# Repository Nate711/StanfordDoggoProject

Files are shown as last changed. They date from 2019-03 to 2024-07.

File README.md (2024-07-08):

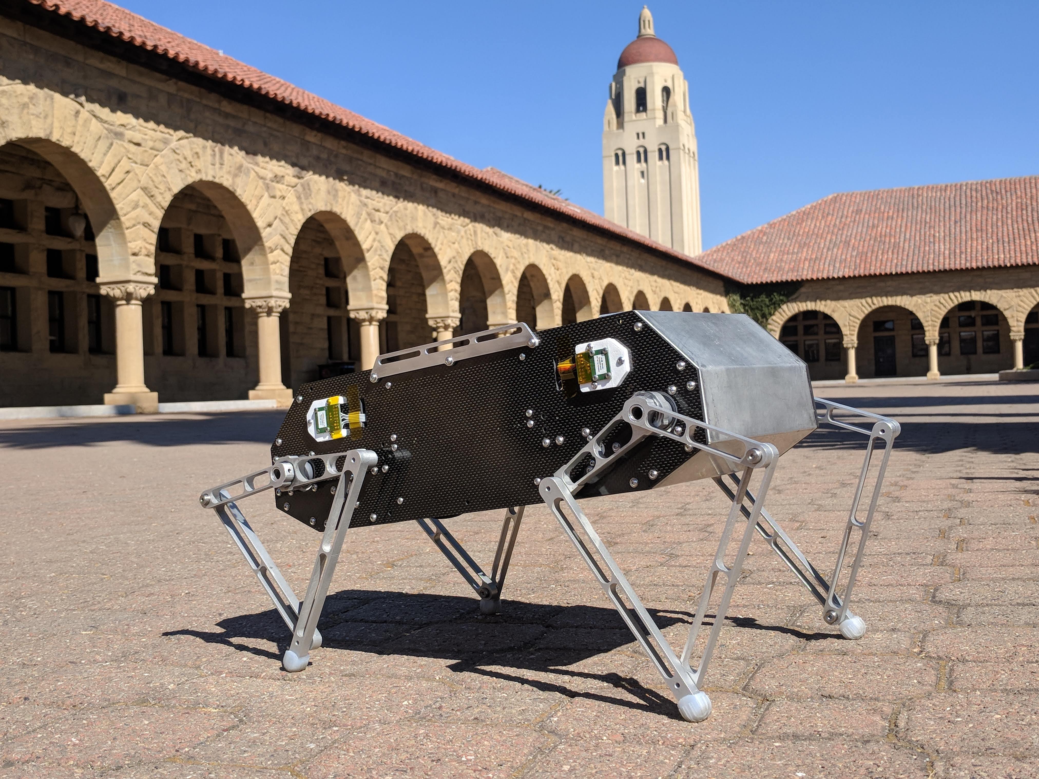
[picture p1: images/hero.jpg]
hero


# End-of-life notice
Thank you everyone for your interest and support over the last 6 years for this project! 

We are hard at work building a new robot, Pupper v3, and so would like to stop supporting this project. Thanks for your understanding! Pupper v3 is fully open source and build instructions will be released in the coming months. You can find preliminary information here https://pupper-v3-documentation.readthedocs.io/en/latest/index.html 







Quick specs for Pupper v3
* Powerful 400W GIM4305 brushless motors
* Raspberry Pi 5
* Reinforcement learning locomotion policy out-of-the-box
* Luxonis SR depth camera
* LCD screen for debugging and facial expressions
* Roughly $1000 BOM

# The Stanford Doggo Project
## Overview Of Stanford Doggo
Stanford Doggo is a highly agile robot designed to be an accessible platform for legged robot research. The robot currently holds the record (among all robots) for the highest vertical jumping agility<sup>1</sup> and can jump twice as high as any existing quadruped robot! Weighing in at a little less than 5kg, Stanford Doggo is easy and safe to develop on, but at the same time, don't expect Stanford Doggo to carry heavy loads or climb super aggressive terrain. If you use a portion of this project or want further technical details, please cite our paper presented at ICRA 2019: https://ieeexplore.ieee.org/document/8794436 (freely available on arxiv: https://arxiv.org/abs/1905.04254). The project is generously supported by Stanford Student Robotics http://roboticsclub.stanford.edu/.

<sup>1</sup>[Vertical jumping agility] = [maximum vertical jump height] / [time from onset of actuation to apogee of jump]

## Building Doggo
We hope you build your own Stanford Doggo! In the Hardware folder of this repository we've linked the Fusion 360 CAD model and it includes all the parts you'll need to source. Many of the custom pieces are either 3d printed or waterjet (instead of manually milled for instance), which means you will only have to do post-processing work. For example, the primary links on each waterjet leg assembly require you to drill and tap a hole for a set screw. If you need help, please reference the CAD, submit an issue to this github repo, or email the owner, nathan kau [at] stanford [dot edu].

You can find a work-in-progress bill of materials here: https://docs.google.com/spreadsheets/d/1MQRoZCfsMdJhHQ-ht6YvhzNvye6xDXO8vhWQql2HtlI/edit#gid=726381752. Please don't hesitate to ask for help!

## Doggo Software
The brains of Stanford Doggo are split between the ODrive motor controllers and the central Teensy microcontroller. To run Doggo, you'll need to flash the our custom ODrive firmware onto the four motor controllers in the robot and then configure them using the doggo_setup.py script included in that repository. Quick note, if you have a different mechanical design than Doggo, make sure to update the gear_ratio parameter in the code or via odrivetool. After uploading the firmware and configuring, you'll next want to upload the Doggo Arduino code to the central microcontroller. This code is responsible for switching between different states and sending the right position commands to the robot. When you power on the robot, the four legs will first do a calibration routine so that the motors and encoders become synced up, and then the robot will enter an idle mode. Once in idle, you can send serial commands over the wireless xbee network to command Doggo to trot, jump, etc. Please reference the Doggo software repo for more information.

## Help
We encourage you to submit issues to this github, or email the owner, nathan kau [at] stanford [dot edu]. 

# A blog post about Doggo
Hi all, I thought I'd share more about the Stanford Doggo Project, which you might have seen in Oskar's New Year's update! We're a group of undergrad and grad students in Stanford Student Robotics and have been working on legged robots for the last year and a half. Our latest robot, Stanford Doggo, is a shoebox-sized quadruped robot that can walk, trot, pronk, and jump around.

I think this video gives the best overview of what Doggo is:

https://www.youtube.com/watch?v=cJxotk4lR90

And my favorite video, Doggo doing a backflip:

https://www.youtube.com/watch?v=aZylPK7SbV0

I&rsquo;ve been seeing a ton of amazing projects here on the forum and on the ODrive Discord channel, so I wanted to make a blog post explaining how Doggo works. I hope people might be able to learn something from this post, and perhaps even build their own Doggo and improve upon it. The whole project is open-source (links below) with CAD, code, and firmware available on Github. The robot code runs on a Teensy 3.5, and we use ODrives for motor control so I imagine a lot of people here could jump right in. We've also tried to make the robot inexpensive to build in your own lab, school, or home, and we absolutely welcome people to contribute to the project. 

## Relevant links:
GitHub project repository: https://github.com/Nate711/StanfordDoggoProject
Full, downloadable Fusion 360 CAD: https://a360.co/2OBxTbH
Teensy code: https://github.com/Nate711/Doggo
ODrive fork: https://github.com/Nate711/ODrive

# Mechanical Design

## Coaxial mechanism
The coaxial mechanism that drives each leg is definitely the most complex mechanical component of the robot. It has also been the most troublesome. The way it works is that we have two TMotor MN5212 motors mounted on the carbon fiber side panel. We also have a 3D printed bearing block that has two bearings to hold the outer coaxial tube. (Refer to the cutaway CAD view below). The two motors transfer power to the coaxial shafts via 6mm wide, 3mm pitch GT2 belts between a 16T pulley and a 48T pulley. We didn&rsquo;t have room in our mass budget for regular, off-the-shelf pulleys, so we printed our own using the Xometry SLS service. As a side note, we learned to always specify to the service that the pulleys must be printed up. If the parts are printed at an angle, the geometry of the pulley teeth gets distorted because of the off-angle layers. Above the pulleys we have a waterjet aluminum bracket to maintain belt tension and thereby prevent skipping during high-torque situations. That said, it was a real pain to find the best center-to-center distance for the bracket because the slop in the connection between the motors and small pulleys, and the slop in the connection between the larger pulleys and the shafts meant that the center-to-center distance for the top bracket had to be 0.5mm larger than the nominal center-to-center distance prescribed by the belt supplier (SDP-SI). The biggest problem with this assembly was that the higher the belt tension, the more friction we had in the assembly. Higher friction means worse tracking performance for the motors, and also worse sensitivity to touch-down events and the like. On our next robot, we&rsquo;re hoping to have smoother, more precisely machined pulleys, and less slop in the coaxial assembly.

#### CAD diagram
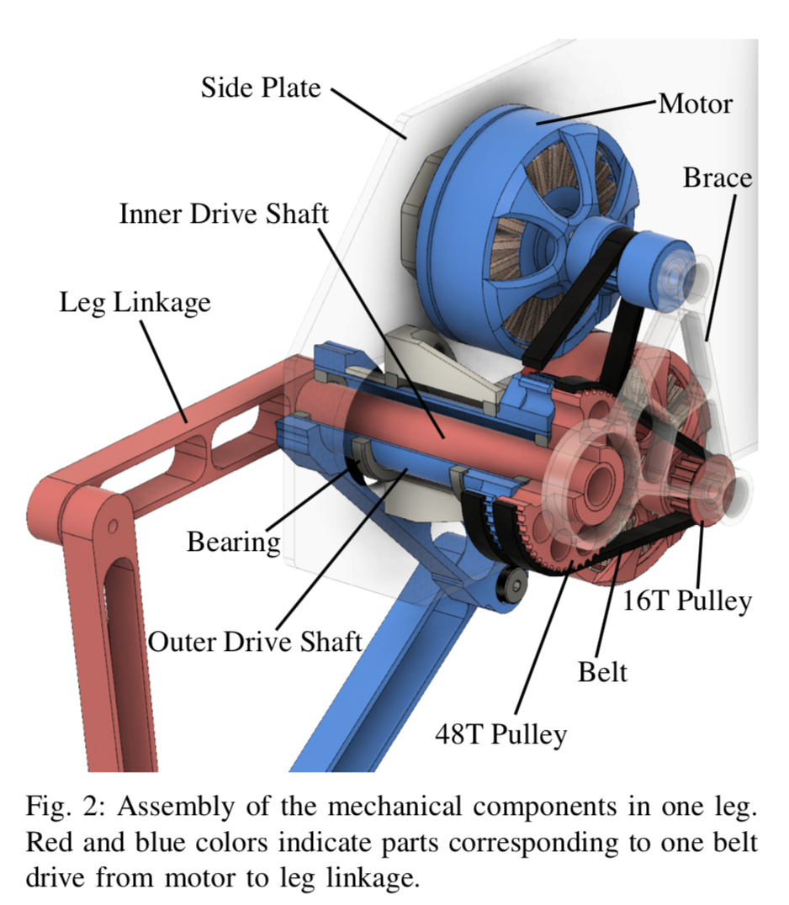
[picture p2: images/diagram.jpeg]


#### IRL
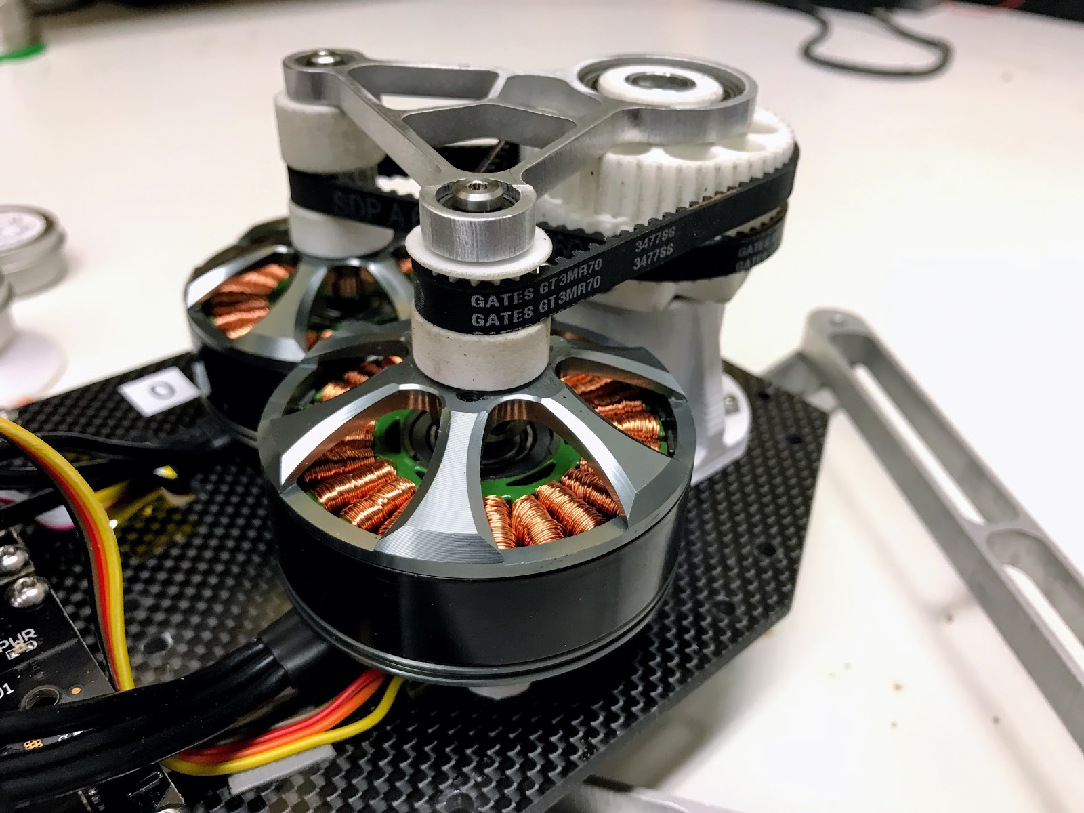
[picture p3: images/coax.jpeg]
diagram


#### In operation
https://www.youtube.com/watch?v=6PL3aur4g4c

## Legs

Doggo has four, 2DOF legs of the SCARA flavor. By SCARA flavor I mean that each leg is a five bar linkage and the two upper links are driven co-axially. The actual leg links were waterjet cut by Big Blue Saw, which is a great online service (although make sure to upload all your parts in one DXF to save money). The waterjet parts were actually precise enough that we did not need to ream the holes for the bearings.

### Joints
For each joint, there are two deep groove ball bearings stacked next to each other in on link, and a shoulder bolt goes through them and threads into the opposing link.

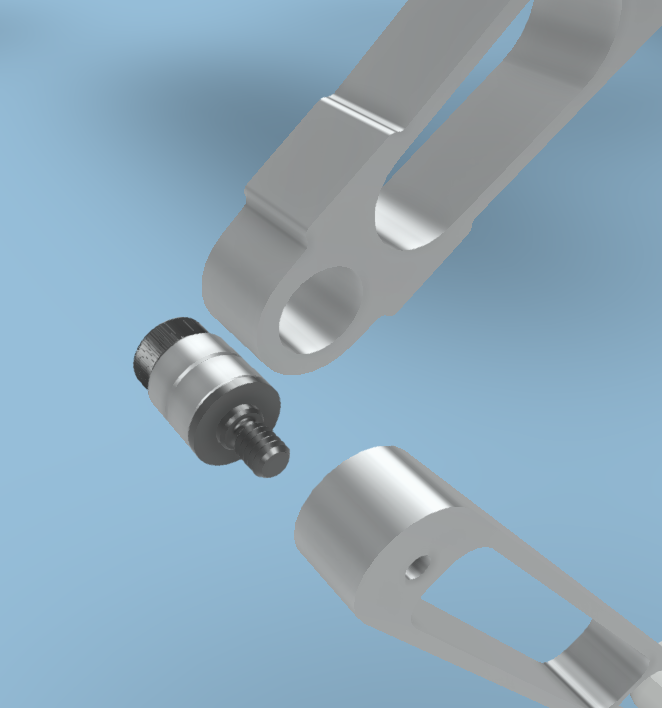
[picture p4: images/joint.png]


### Feet
The robot feet are silicone pieces that we made using a 3D printed, 2-part mold.

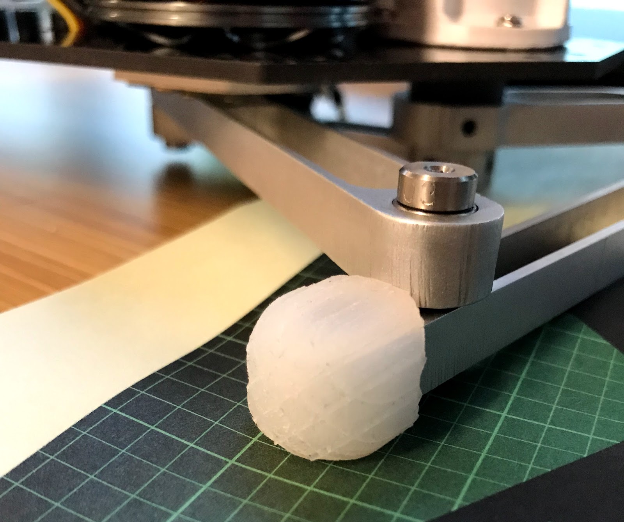
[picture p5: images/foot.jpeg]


## Frame

The frame of the robot is thankfully very simple. We have two waterjet, 4mm carbon fiber panels on each side, connected by two 1/32&rdquo; 5052 aluminum sheet metal parts. These sheet metal parts were cut using a waterjet, and then folded up by hand (long story, but because the two carbon fiber panels are canted inwards, the tabs on the aluminum part couldn&rsquo;t be folded on a brake).

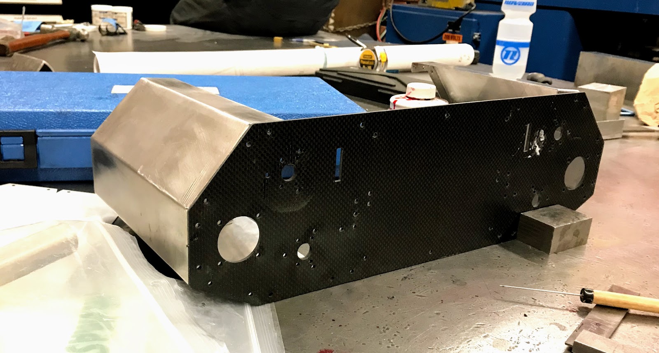
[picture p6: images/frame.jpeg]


# Electronics
Doggo has four v3.5, 48V ODrives, two for each leg, mounted on the carbon fiber side panels. Sitting on a 2mm carbon fiber plate in the middle, we have a Teensy 3.5, a Sparkfun BNO080 IMU, and a 5mW Xbee. The Teensy talks to the ODrives over four separate UART lines, each operating at 500,000 baud. Underneath this plate, we have the power distribution board (a janky quadcopter PDB we found on Amazon), and a fancy Gigavac P105 Mini-Tactor relay so we can kill the robot power using an offboard ESTOP switch. We also put our two, 1000mah 6s Tattu lipo batteries down there.

Last, but not least, each motor has a AS5047P encoder to track the motor angle. We actually are only using the incremental interface, because at the time we built the robot, there was no absolute encoder support on the ODrive and we couldn&rsquo;t make the index pin functionality work either.

#### Electronics schematic
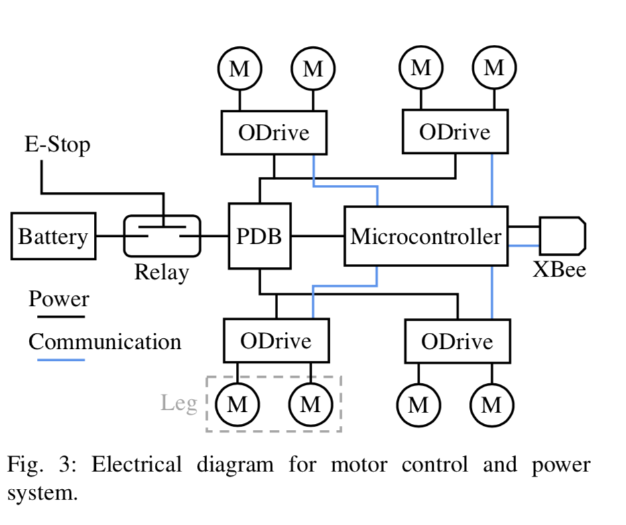
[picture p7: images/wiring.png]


#### Layout of ODrives
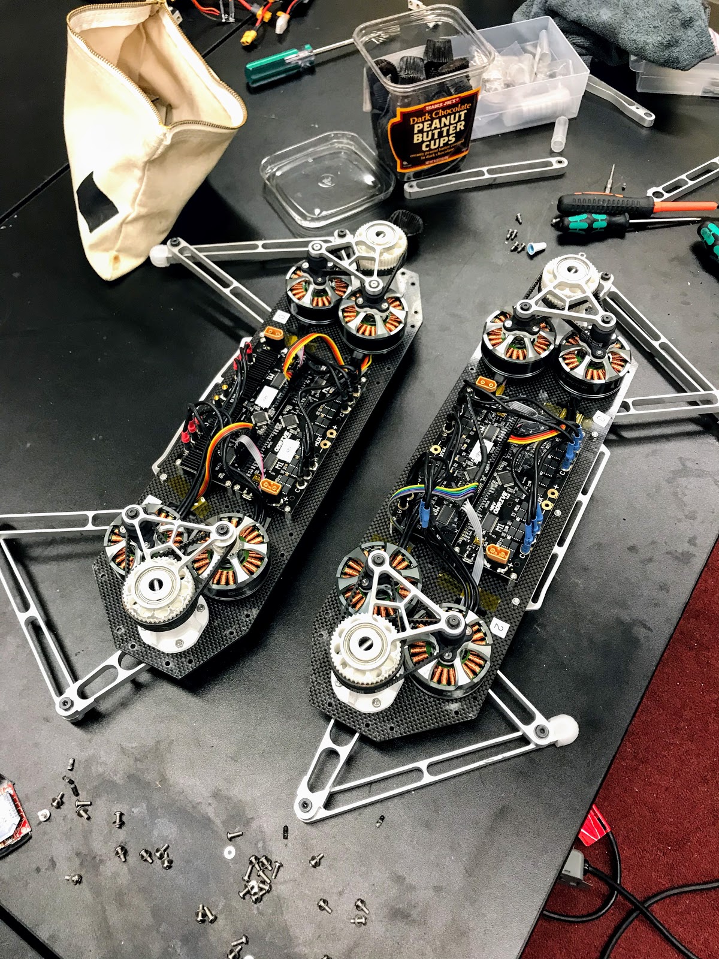
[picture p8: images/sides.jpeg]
|394x526


#### Top side of the middle electronics plate
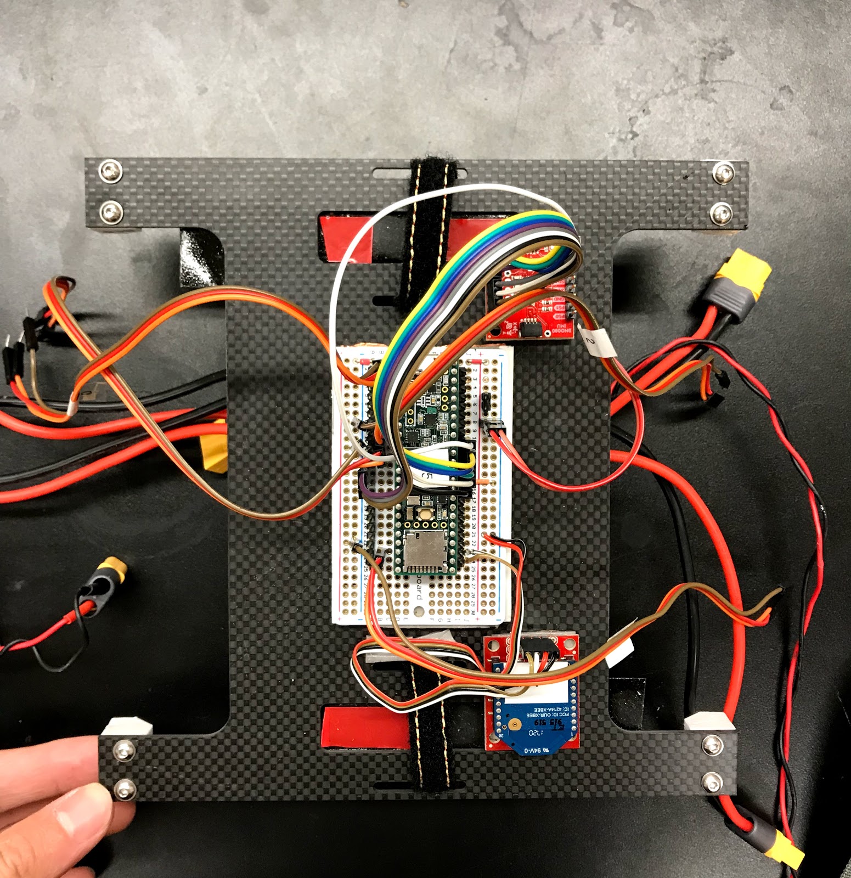
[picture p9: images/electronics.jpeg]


#### The belly of the robot: Relay (translucent piece in the middle), PDB (golden board in front of the relay), and batteries (close and far).
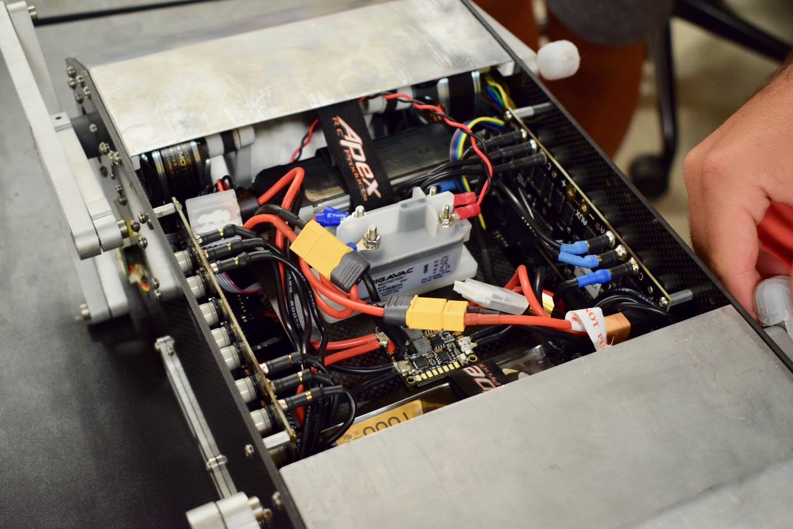
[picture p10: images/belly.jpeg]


# Software

## Overview

The Doggo software is relatively simple as far as things go. The gist of it is that we have a state machine that flips between different behaviors (like trot, jump etc), and for each behavior we send different position commands and gains to the four ODrives. We also have some helper threads running, like one to take IMU measurements, another to record telemetry from the ODrives, another to take commands over Xbee, etc.

## Leg trajectories

The robot walks, trots, bounds, and pronks by commanding different sinusoidal open-loop trajectories to the four ODrives. The leg trajectories are composed of two halves of sinusoidal curves for the flight and stance phases shown in orange and purple in the picture. The geometric parameters of the sinusoids, the virtual leg compliance, and the duration of time that the leg spends traversing each sinusoidal segment, were varied to create different gaits.

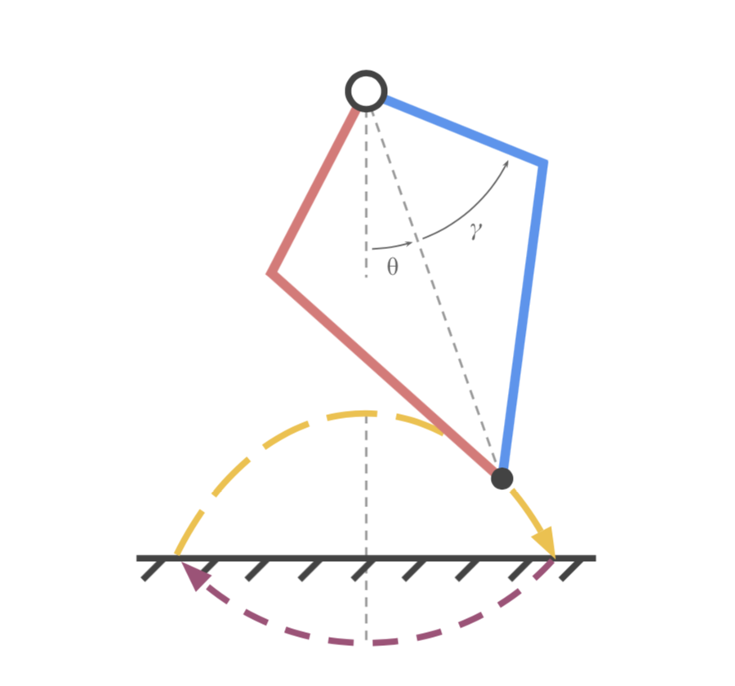
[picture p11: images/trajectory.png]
|265x299


At any given time, the Teensy computes the desired foot locations in cartesian coordinates, and then converts them to leg angles (θ) and leg separations (γ). These two numbers describe the virtual leg that originates at the hip joint of the leg and terminates at the foot.

These virtual leg parameters (theta and gamma) and their corresponding virtual stiffness and damping coefficients are sent from the Teensy to the four ODrives at the 100Hz refresh rate. The ODrives then run a custom PD controller to generate torques in theta-gamma space. The ODrives then use the [Jacobian](http://robots.iit.edu/uploads/2/5/7/1/25715664/mmae_540_-_lecture_2_-_manipulator_kinematics.pdf) of the leg to transform torques in theta-gamma space into torques in the motor0-motor1 space.

## ODrive Control
We implemented a custom binary UART protocol to send and receive data. The binary protocol is significantly faster than the ASCII protocol, which (I think) was the only protocol implemented for the Arduino when we built the robot. If you'd like more of the specifics, visit https://github.com/Nate711/Doggo/blob/master/lib/ODriveArduino/ODriveArduino.cpp

**I think that about wraps everything up! Let me know if you have questions, and I&rsquo;ll also try to update the post if people are interested in more details.**

# FAQ
## The sub-folders are empty!
Run this to populate the folders.
```shell
git submodule update --init --recursive --remote
```
## How do I configure the ODrive parameters for Doggo?
We use the script ```https://github.com/Nate711/ODrive/blob/master/tools/doggo_setup.py```
## How are the legs numbered?
Leg0 is the front left, leg1 is the back left, leg2 is the back right, and leg3 is the front right.
## How do I calibrate the legs?
This is a sore spot for the robot right now. When you power on the robot, all the driven linkages (ie top links) need to be as horizontal as possible. If everything is set up correctly, the motors will then begin their calibration routine which involves them rotating about 120 degrees to one side and then back. After this, the robot is ready.
## Can it turn?
Yes and no. It turns very slowly with the 'Y' command. The turning speed is set by 's [desired step difference]' where the step difference should be around -0.1 to 0.1 at the most.
## Which way should the IMU point?
There are little markings on the BNO080 board which indicate which way x is positive. Align that direction with the forward direction of the robot. The forward direction is towards the motors connected to ODrives 0 and 3. 
## How are the ODrives connected to the Teensy?
We use serial connections between the Teensy and ODrives so for each ODrive you'll need to connect Teensy RX to ODrive TX and Teensy TX to ODrive RX. Since there are four ODrives, you'll have to connect up four sets of these serial connections!

In code we have these definitions which may help with wiring:
```cpp
HardwareSerial& odrv0Serial = Serial1;
HardwareSerial& odrv1Serial = Serial2;
HardwareSerial& odrv2Serial = Serial3;
HardwareSerial& odrv3Serial = Serial4;
```

Here's also a little chart made by HelloPlanet!
```
Teensy3.5 --- Logical Function --- Component
P0 - RX1 - ODrive1 (odrv0)
P1 - TX1 - ODrive1 (odrv0)

P7 - RX3 - ODrive3 (odrv2)
P8 - TX3 - ODrive3 (odrv2)

P9 - RX2 - ODrive2 (odrv1)
P10 - TX2 - ODrive2 (odrv1)

P31 - RX4 - ODrive4 (odrv3)
P32 - TX4 - ODrive4 (odrv3)
```
## How is the Xbee wired?
We connect it via serial to Serial5. We also have a definition in ```config.h``` called ```USE_XBEE``` that determines whether the code should use the actual USB port on the Teensy or the Xbee for communications. 
## How is the IMU wired?
We connect it via SPI with the following defines.
```cpp
//Pins for BNO080 IMU
#define SPI_CS_PIN 15
#define SPI_WAK_PIN 14
#define SPI_INTPIN 17
#define SPI_RSTPIN 16
```
## How does the relay get wired up?
We now use a solid-state relay https://www.digikey.com/product-detail/en/sensata-crydom/D06D100/CC1520-ND/353618 with the output terminals in series with the main power and the input terminals connected to an external battery with a switch. We have the switch wired up in serial so that pressing the switch will turn on/off the relay and thus the robot's main power.
## The CAD doesn't download correctly
This is unfortunately not a problem on our end but on Fusion's. Fusion customer service has in the past been able to fix corrupted uploads on their server.

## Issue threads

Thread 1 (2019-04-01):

BoM information

ZiadJ, 2019-04-01:
Is there any information available on the costs involved in building this little machine? I heard from the video that it wouldn't be more than $3k which is well above what the average tinkerer can afford. I'm not sure what exactly would justify the costs of the current setup but I'm hoping that having some information about it would help figure out how to lower the costs eventually for less demanding environments.

CrazyAZ, 2019-04-03:
We have a [BOM spreadsheet](https://docs.google.com/spreadsheets/d/1MQRoZCfsMdJhHQ-ht6YvhzNvye6xDXO8vhWQql2HtlI/edit#gid=726381752) which gives a break down of the cost.  And I'd be happy to give a few thoughts on how it could be made cheaper.

The two most expensive items are the motors and motor controllers, which would be hard to replace, but after that come the custom parts.  We calculated our cost assuming that these custom parts would be outsourced, allowing Doggo to be built by anyone with common hand tools.  However, if you have access to a 3D printer or waterjet cutter you can produce these parts for cheaper than if you pay another service to make them for you.

With that said, an SLS 3D printer and waterjet cutter are likely not accessible to the average tinkerer either.  So the following are some possible ways you could get around needing these expensive pieces of equipment, but I cannot guarantee how well they will actually work.

First, the pulleys could be printed with a more standard and cheaper 3D printer.  The worry is that the tolerances may not be very good and the timing belts may not fit as well.

You could also try replacing the waterjet parts with laser cut parts.  This would require a pretty significant change in the materials these parts are made of since carbon fiber and aluminum can't be laser cut, and replacing these materials will result in significantly weaker parts.  The only laser cuttable material I know of that is even close to these in durability is delrin, which is also pretty expensive and may or may not actually save you money.  There are certainly cheaper materials you could try, but your parts may break while operating the robot.

I hope this helps.  Let me know if you have any more questions.

Closed 2019-04-22.

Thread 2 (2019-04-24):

Minor design flaw in CAD

zebrassimo, 2019-04-24:
Hi gents, while trying to get myself confident with the design (maybe I want to rebuild doggo :-), I found this:

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
blue: SDP intersects with Outer Leg Shaft
red: SDPs intersect with each other

I trust you have fixed this after printing.

CrazyAZ, 2019-04-24:
It's great to see interest in rebuilding Doggo.

It appears that your CAD is using two inner shaft pulleys, when instead there are separate pulleys for the inner and outer shaft.  The CAD should look like this:
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
And the pulley that goes on the outer shaft looks like this:
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
As far as I can tell this is what is in our distributed full CAD, but if you still think there's an issue I can look into it.

Hope this was helpful. Let us know if you have any more questions.

zebrassimo, 2019-04-24:
Thanks Aaron! I had just downloaded the cad files from the source link (need to check, it‘s already late in Germany). The issue seems to be a version conflict between your internal files and the published ones.

    	Outlook für iOS beziehen

On Wed, Apr 24, 2019 at 9:06 PM +0200, "Aaron Schultz" <notifications@github.com> wrote:

It's great to see interest in rebuilding Doggo.

It appears that your CAD is using two inner shaft pulleys, when instead there are separate pulleys for the inner and outer shaft.  The CAD should look like this:

And the pulley that goes on the outer shaft looks like this:

As far as I can tell this is what is in our distributed full CAD, but if you still think there's an issue I can look into it.

Hope this was helpful. Let us know if you have any more questions.

—
You are receiving this because you authored the thread.
Reply to this email directly, view it on GitHub, or mute the thread.

It's great to see interest in rebuilding Doggo.

It appears that your CAD is using two inner shaft pulleys, when instead there are separate pulleys for the inner and outer shaft.  The CAD should look like this:
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
And the pulley that goes on the outer shaft looks like this:
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
As far as I can tell this is what is in our distributed full CAD, but if you still think there's an issue I can look into it.

Hope this was helpful. Let us know if you have any more questions.

--
You are receiving this because you authored the thread.
Reply to this email directly or view it on GitHub:
https://github.com/Nate711/StanfordDoggoProject/issues/2#issuecomment-486385538

zebrassimo, 2019-04-25:
So I figured that the link https://a360.co/2OBxTbH leads me to the browser view and here it's fine:
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
When I download the Fusion360 archive (email required) I receive a file called Full Doggo CAD.f3z which which is binary the same as the one I uploaded into my Fusion360 which caused the issue initially mentioned.

Well, never mind I'll get alog with this.

maxsu, 2019-08-10:
I've checked all four sets of inner and outer pulleys in the v1.0 doggo hardware model (https://a360.co/2OBxTbH), and they look correct:
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

This looks like it is internal revision 3:

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
Therefore I can only guess that the issue was caused by one of:

A) There is some earlier, publicly available revison that shows @zebrassimo's issue
B) There was some import glitch or other error on @zebrassimo's side

I believe that Fusion 360 Public Links point to the latest revision of a design, which would technically allow A) to happen. However @zebrassimo's 'same binary' comment makes me give more weight to B).

It would be useful to gain insight on the CAD environment that caused the issue. However, if there is no replication then this issue seems closed.

 @zebrassimo, what CAD software did you import into? Have you been able to replicate the issue since?

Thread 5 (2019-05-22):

Voltage information

netphreak0101, 2019-05-22:
Looking though the docs and the BOM, I'm trying to see the voltage needed to drive the motor controllers. You referenced 48v on the git, but the motor drivers are only 24v. Are you driving each controller through a separate battery? Do you have a better wiring schematic?

CrazyAZ, 2019-05-23:
The ODrive motor controllers that we use support up to 48V, but can also be run on a power supply as low as 12V.  In our design we run two 24V batteries in parallel, which supply power to the entire system.

CS4Liu, 2019-07-19:
So do the 24v version of ODrive motor controllers work well too?

UPUPGOO, 2020-01-02:
> So do the 24v version of ODrive motor controllers work well too?

In my test(24 version), when you conduct the 'backflip' command, the torque is not big enough. And the doggo failed to do a backflip. So I decide to use 48v version of ODrive.

Closed 2019-05-25.

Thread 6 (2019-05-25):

Where is pcb?

790947648, 2019-05-25:
Hello, I really like this open source project, I want to know how to find the PCB? I am in China, I think my manufacturing costs are lower.

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

CrazyAZ, 2019-05-25:
Those PCBs were not created by us.  We purchased them from ODrive, so we do not have the design for them. You can find more information about them here: https://odriverobotics.com/

790947648, 2019-05-25:
Thank you~

Closed 2019-05-25.

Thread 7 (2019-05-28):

How did you machine the pulley brace?

mengqlTHU, 2019-05-28:
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
First thank you very much for making the doggo open source.
I am a little confused because this pulley brace seems to have two version: the aluminum one and the ABS plastic one. Which one are you using in the current version? And how did you assemble this part with the bearings? Thanks.

ZhangLiangShan, 2019-05-28:
According to my understanding, this is just a three-shaft positioning assembly, ensure the parallelism between the three-shaft. I used 6061 aluminum alloy processing, which is not cheap, it cost me 1100 RMB

Nate711, 2019-05-28:
Hi there, we actually 3d printed that item for the second Doggo we built. It was just cheaper and the aluminum wasn't necessary. The bearings were press-fit in with some super glue.

Closed 2019-05-28.

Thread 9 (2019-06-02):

Regarding current flow amperage of each motor

HelloPlanet, 2019-06-02:
Hi Nate and team,

I'm trying to build a doggo here, while checking ODrive part, I found that the battery have a peak working current of 75A, each battery supplies four motors. But banana connectors from ODrive to motor is 3.5mm which allow 30A continuous current. This is a bit unclear to follow.

Do we have any test results on how much cuurent each motor draw from the drive? Thanks.

Edit:
Also, I found it hard to figure out how the battery power is distributed to PDB and ODrive boards.
As I have experience working with quadcopter, I can think of some schemes that work, but still, i'm curious how you guys will distribute battery power.

My idea:
Battery#1
.....|
Contactor
.....|-PDB
.....|--ODrive#1
.....|--ODrive#2

Battery#2
.....|--ODrive#3
.....|--ODrive#4

Is this correct?

Nate711, 2019-06-03:
Hi there. Thanks for your diligence! The peak current drawn by the motors is around 40A and the average is around 5A so the 30A continuous limit on the bullet connectors is completely fine.

For the electronics wiring, please reference the README for this project which includes a little diagram on how everything goes. Basically the two batteries are connected in parallel to the PDB, which then powers the four ODrives. It's very much like a quadcopter setup except that we have two batteries in parallel going to the PDB instead of just one.

HelloPlanet, 2019-06-03:
Thanks Nate, that explained everything.

790947648, 2019-06-04:
Looking forward to seeing your second edition of Doggo

Closed 2019-06-03.

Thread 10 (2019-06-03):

About the belt model

rabbit-zc, 2019-06-03:
First thank you for making the doggo open source.
Then,My friends and I are planning to make one.
Now I want to check if the belt is this model:

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

thank you
Looking forward to your reply

Nate711, 2019-06-03:
That's the one! Let me know when you get to fabricating the coaxial tubes because I might have some ideas on how to make it easier on you guys.

Nate711, 2019-06-03:
By the way if the GT2 belts are out of stock, the GT3 belts will work as well.

rabbit-zc, 2019-06-05:
OK,thank you.

Closed 2019-06-03.

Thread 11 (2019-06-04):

T-Motor MN5212 Not Available

danbo2, 2019-06-04:
Hi,

The suggested T-Motor MN 5212 is currently unavailable in Amazon. Can you give another one to replace it?

Thanks,
Yiyi

HelloPlanet, 2019-06-04:
I‘m not from Project Doggo team, but as far as i know, you can find other 5212 304KV motors in stead.

The key specs you may want to check are as follows,
340KV -- this has to be specific
35A 840W max continuous power -- this could be a bit different
dims: Shaft 6mm, Stator 52mm x 12mm -- this better be specific, especially the shaft and axis size
motor 59 x 33.5mm -- this is the outer dimension and will not affect much, as long as the stator and axis is at same place, but if you had a motor much bigger in outer dimension, it may not fit in the relatively tight space inside Doggo.

No. of Cells (Lipo): 4-8S -- this will decide the working voltage range of the motor. as far as i know, all 5212 motors should be in this range.

Nate711, 2019-06-13:
Thanks HelloPlanet for answering the question! You can definitely make Doggo work with a variety of motors, but if the dimensions are different then you'll probably have to modify the mechanical design. Your best bet is to buy the T-Motor 5212 motors which you can also find at:
http://store-en.tmotor.com/goods.php?id=377
https://www.foxtechfpv.com/tmotor-mn5212-kv340.html

I hope they become available again on Amazon since they tend to be listed at a cheaper price there.

danbo2, 2019-06-13:
Thanks. It works.

Closed 2019-06-13.

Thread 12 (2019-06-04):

Linkage foot silicone rubber hardness?

HelloPlanet, 2019-06-04:
Hi Nate and team,

As i have mentioned, I'm working on building a Doggo. (Yay! Thanks!)

While choosing silicone material for Doggo's feet,
 I noticed the silicone rubber in BOM, Dragon Skin™ 30,
has a hardness of Shore Hardness 30A.

As i haven't placed order yet, the options I have is from 30A to 90A.
Do I need to choose harder or softer rubber? Please advise. Thanks!

Nate711, 2019-06-13:
Sorry HelloPlanet for the delay! I would recommend the softer 30A rubber. Thanks!

Closed 2019-06-13.

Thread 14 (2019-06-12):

When we clone the project, the folders are empty, could you please solve the problem?

mohakhalili71, 2019-06-12:
I want to use your project. But unfortunately, when I clone the project, I will encounter empty folders. All folders are empty, except the photos folder. Please check this problem.

Thank you for helping me.

maxsu, 2019-06-12:
This project uses git submodules, which can be initialized by performing

> git submodule update --init --recursive --remote

This populates the subdirectories:

```
~/src/StanfordDoggoProject$ tree -L 2
.
├── Doggo
│   ├── lib
│   ├── platformio.ini
│   ├── README.md
│   └── src
├── DoggoHardware
│   └── FullCAD
├── images
│   ├── belly.jpeg
│   ├── coax.jpeg
│   ├── diagram.jpeg
│   ├── electronics.jpeg
│   ├── foot.jpeg
│   ├── frame.jpeg
│   ├── hero.jpeg
│   ├── hero.jpg
│   ├── joint.png
│   ├── sides.jpeg
│   ├── trajectory.png
│   └── wiring.png
├── LICENSE
├── ODrive
│   ├── analysis
│   ├── Arduino
│   ├── CHANGELOG.md
│   ├── docs
│   ├── Firmware
│   ├── ODrive_Workspace.code-workspace
│   ├── README.md
│   └── tools
└── README.md
```

Hope this helps you get doggoing 😉

mohakhalili71, 2019-06-12:
Thank you Max, it does work now.

Nate711, 2019-06-13:
Thanks so much Maxsu for answering that question!

Closed 2019-06-13.

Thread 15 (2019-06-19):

how to use microcontroller to read encoder data from Odrive?

csyyzhang, 2019-06-19:
Hi. Nice job! I have a problem with using microcontrollers to communicate with Odrive. I try to read encoder data by following the example given in the Odrive Arduino library. However, no matter what happens, whether the motor is moving or not, the return data is always 0. I have checked the connections by using the Odrive tool for PC, and it can read the encoder data properly. Do you have any suggestions for me? Thanks.

Nate711, 2019-06-24:
Hi there, could you post your code and maybe a picture of your wiring setup? Thanks!

Closed 2019-07-10.

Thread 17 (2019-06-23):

Some Detailed Questions about Doggo's PDB

charemax, 2019-06-23:
Hi，My mentor and I are very interested in your doggo project. Can you tell me the details about Odrive's PDB?Which type of PDB is it?

kigerzh, 2019-06-24:
It was listed in the BOM :  "Makerfire FCHUB-6s"
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

Nate711, 2019-06-24:
Thanks for the reply Kigerzh!

Closed 2019-06-24.

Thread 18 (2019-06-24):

BOM map to CAD

kigerzh, 2019-06-24:
Dear Aaron,
Thanks so much for the great project.
Now I am plan to rebuild the Doggo .  I checked the BOM ,but it is hard to map with the CAD,due to missing  uniqe component ID. Especially  for some small objects. For example in CAD,  what is  the object under encoder?  :  Full Doggo Assembly v170/single plate design v471:1/AS5048A v26:4/Component2:1

Is it possible to  export  a BOM from the CAD  and then  you give some comment in that BOM ?   Or  add more information in the CAD file .

HelloPlanet, 2019-06-27:
As a matter of fact, i'm combing the whole CAD file to build a new BOM....

SunHR-SWJTU, 2019-07-12:
The object under AS5048A looks like the magnet of encoder.

maxsu, 2019-07-19:
I'd love to help revise the bom / make it more accessible. I'm working in Rhino. Ideas are welcome!

bestjinx, 2019-08-09:
Thank you very much for your work. Now we want to reproduce your project, but I find that there seems to be no complete circuit connection schematic in the files you uploaded, so I hope you can upload it if it's convenient. Thank you very much

YANGKAI-MAX, 2020-01-16:
I haven't found the general assembly drawing. Who can help me?

YANGKAI-MAX, 2020-01-16:
I haven't found the general assembly drawing. Who can help me?

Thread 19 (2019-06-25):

Unknown component in CAD

kigerzh, 2019-06-25:
what is the object under encoder?  Is it  magnet ?     Its path in the CAD  : Full Doggo Assembly v170/single plate design v471:1/AS5048A v26:4/Component2:1

HelloPlanet, 2019-06-27:
I'm trying to figure this out, too.
As far as i understand, that would be a magnet needed for use with AS5048A magnetic encoder.

Nate711, 2019-07-01:
Yup! The magnet comes with the AS5047D encoder (or equivalent encoder), and you superglue it to the rear shaft of the MN5212 motor.

Closed 2019-07-01.

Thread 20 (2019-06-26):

Is there specific wiring schemetics?

sihanwang-eng, 2019-06-26:
Amazing project！

Where can I find the specific wiring schematics diagram? I'm a bit confusing about the wiring things such as how to connect the Teensy Controller with the four Odrives.

HelloPlanet, 2019-06-27:
You can find wiring information from both source code and picture in readme.md

**_Following are my study, not from Doggo Project Team, use at your own risk!_**

Teensy3.5 --- Logical Function --- Component
P0 - RX1 - ODrive1
P1 - TX1 - ODrive1

P7 - RX3 - ODrive3?2
P8 - TX3 - ODrive3?2

P9 - RX2 - ODrive2?3
P10 - TX2 - ODrive2?3

P31 - RX4 - ODrive4
P32 - TX4 - ODrive4

Closed 2019-07-10.

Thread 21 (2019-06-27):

Wondering about the reasoning behind part selections

askewc, 2019-06-27:
Awesome project! I'm looking to take a crack at building Doggo, but as $3k is a lot for a humble hobbyist, I'm looking to cut costs/reuse parts I already have. It'd be great to know _why_ you chose certain parts, so I can understand what I'm trading off.

- Motors
  - ~$800 is a lot! Are there specific advantages to using the T-Motor MN5212 KV340 over motors with the same stator size from another brand? Are there other ways one could cut cost here?

- Legs
  - Why do they need to be aluminum? I'd guess it has something to do with handling high torque, like with the braces-- if so, are there many scenarios in which the legs would be so stressed (besides jumping / falling)?
  - [MIT's Super Mini Cheetah](https://www.youtube.com/watch?v=CEAfiyreL9E) walked around on plastic legs. No backflips, though :)

- ODrive Controllers
  - I have some SaberTooth and RoboClaw motor controllers from some old projects. How does ODrive outperform its contemporaries?
  - (although honestly, are my controllers even comparable? They're so much fatter than the ODrive)?

Thanks again for sharing your work and taking questions!

HelloPlanet, 2019-06-27:
Just FYI, i ordered fiber glass 3D printed legs out of curiosity, and they have no match in strength to 6061 aluminium.
Should you really would like to cost down the project, please consider reconstruct the foot linages.

As for ODrive. I think the team stated in readme that they need ODrive to have close loop control of the motor. That is, they leave the whole motor speed sensing, controlling and feedback thing to ODrive thus allow Teensy to focus on sensing and controlling the attitude of the whole Doggo.

Nate711, 2019-07-01:
Hi askewc!

1) The motors are probably the best spot to look for cost savings, but it's not trivial to swap in a different motor because of varying  geometry. As for alternate motors, you can really use any motor with a similar torque rating, which in most cases means finding a motor with the same or larger stator geometry (5212). However, a different motor will nearly certainly have slightly different geometry, which means you will have to adjust the encoder mount to adapt to the new magnet<->encoder distance, and the pulleys to accommodate the different rotor height.

2) The legs definitely do not have to be made of aluminum, but if you choose to make them out of 3D printed nylon for instance, you will certainly have to strengthen the parts and you may also have to come up with a solution to transferring torque between the coaxial shafts and the links that attach to them.

3) ODrive is as cheap as you can get right now for the functionality it offers. I think a truly inexpensive quadruped robot may only be achievable with servo motors. I hope someone makes that soon!

Closed 2019-07-01.

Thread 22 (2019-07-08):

How to place IMU board

kigerzh, 2019-07-08:
Hi Nathan,
How to place the IMU board:  the X point to head or Y point to head?

HelloPlanet, 2019-07-09:
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

as you can see in this picture,
the "front" direction Doggo heading to is X, to his "left" is Y, and the direction to ground is Z.

or maybe i can misunderstood front and back, but i don't think it will matter much, as Doggo is symmetric.

CrazyAZ, 2019-07-10:
The photo of our electronics plate that @HelloPlanet posted is going to be the best reference as to how we oriented ours.  However, the direction the imu is pointing in the picture is actually with Y pointing forward.  With that said, you can orient it any way you want as long as the pitch is calculated using the right gyro axis in imu.cpp.

Closed 2019-07-10.

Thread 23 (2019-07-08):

The output value of the encoder fluctuates greatly！！

UPUPGOO, 2019-07-08:
Hi. It is a nice job. I am trying to make a doggo, but I meet a problem. I am using AS5047P as the encoder, but the output value of the encoder changes a lot. For example, if I set the position at 1000, the output value fluctuates around 1000 and the fluctuation range is around 50. I find the motor jittering. Is it normal? How can I stop it? Now, I am ready to buy the shielded wire. Maybe, it will work. I need your help.

HelloPlanet, 2019-07-09:
Please consider post a photo of your setup.
As per AS5047P manual said, the space between the magnet and sensor chip should be 0.5-3mm.

CrazyAZ, 2019-07-10:
Unfortunately, without more information this is going to be hard to diagnose. One thing I would check is if these fluctuations occur when the motor is not being controlled.  If not, it may be that your kp gain for the PID control is too high. This would cause the motor to constantly over shoot its target and jitter.

Closed 2019-12-05.

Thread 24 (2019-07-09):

Whitch arduino project is the main process to analysis the serial commands let doggo run  jump?

xuankaicheng, 2019-07-09:

CrazyAZ, 2019-07-10:
All the code for handling the serial commands sent to the teensy is in the file usb_serial.cpp

Closed 2019-07-10.

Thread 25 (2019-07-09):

Custom ODrive Firmware build with binary protocol?

HelloPlanet, 2019-07-09:
Hi Nate and team,

I've cloned your fork of ODrive software from this repo, and was trying to build the "custom binary protocol firmware" and flash it to my ODrives.

Upon building, the config file says
`CONFIG_UART_PROTOCOL=ascii`

do i need to change this, or should i just build and flash with default config?

Thanks.

CrazyAZ, 2019-07-10:
The uart protocol being set to ascii is indeed correct. Our custom communication protocol transmits the values to the odrive as if they are ascii characters, and then our firmware knows to interpret the binary representations of those characters as floats instead.

It's been a while, but I believe we did this as a way to allow the sending multiple values at a time.  The ascii protocol is far less strict about the size of the messages, giving us more flexibility than the native binary protocol.  However, because we send the values in their binary form instead of as ascii characters it is significantly faster than the original ascii protocol.

HelloPlanet, 2019-07-10:
Thanks for your detailed explanation!

mengqlTHU, 2019-07-30:
@HelloPlanet Have you successfully run the code? I think I have compiled and uploaded the ODrive and Teensy firmware correctly, but when I send command to teensy, the motor just does not move at all.

Closed 2019-07-10.

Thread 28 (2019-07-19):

Some problem in ODrive config.

JacobShenHdu, 2019-07-19:
Hi, I had some trouble in Odrive config. I run "full_calibration"(odrive/tool/doggo_setup.py) and test motor by "set_pos_position" like this:
odrv.axis0.requested_state = AXIS_STATE_CLOSED_LOOP_CONTROL
odrv.axis1.requested_state = AXIS_STATE_CLOSED_LOOP_CONTROL
time.sleep(3)
odrv.axis0.controller.set_pos_setpoint(2000.0, 0.0, 0.0)
odrv.axis1.controller.set_pos_setpoint(2000.0, 0.0, 0.0)
time.sleep(3)
odrv.axis0.controller.set_pos_setpoint(0.0, 0.0, 0.0)
odrv.axis1.controller.set_pos_setpoint(0.0, 0.0, 0.0)
time.sleep(3)
odrv.axis0.controller.set_pos_setpoint(-2000, 0.0, 0.0)
odrv.axis1.controller.set_pos_setpoint(-2000.0, 0.0, 0.0)
time.sleep(3)
odrv.axis0.controller.set_pos_setpoint(0.0, 0.0, 0.0)
odrv.axis1.controller.set_pos_setpoint(0.0, 0.0, 0.0)
time.sleep(3)
odrv.axis0.controller.set_pos_setpoint(4000.0, 0.0, 0.0)
odrv.axis1.controller.set_pos_setpoint(4000.0, 0.0, 0.0)
time.sleep(3)
odrv.axis0.controller.set_pos_setpoint(0.0, 0.0, 0.0)
odrv.axis1.controller.set_pos_setpoint(0.0, 0.0, 0.0)
time.sleep(3)
odrv.axis0.controller.set_pos_setpoint(-4000, 0.0, 0.0)
odrv.axis1.controller.set_pos_setpoint(-4000.0, 0.0, 0.0)
time.sleep(3)
odrv.axis0.controller.set_pos_setpoint(0.0, 0.0, 0.0)
odrv.axis1.controller.set_pos_setpoint(0.0, 0.0, 0.0)

But the motor sometimes will go crazy and the vel_limit doesn't seem to work. I exchanged the connection of two motor and ODrive, but the motor still go crazy randomly, and not sure which one will. It seems problem is not enconder failure. When I config single axis of ODrive, there is no problem.
And I also don't understand what's the difference between the flag "startup_encoder_index_search" and "startup_encoder_offset_calibration".

Closed 2019-08-02.

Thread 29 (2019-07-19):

Error when open the fusion model version2

CS4Liu, 2019-07-19:
Hello,I try to use Autodesk Fusion 360 to open the fusion model version2 for more details of Doggo.But when I upload the 'Full Doggo Assembly.f3z' in the Autodesk Fusion 360 the error comes:

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
Do know how can I solve this problem？
Thanks!

CrazyAZ, 2019-07-31:
I see that you have closed this issue. Did you find a solution to it? Someone else is having the same problem, but I cannot find anything wrong in the CAD.

CS4Liu, 2019-07-31:
I didn't find solution to it. There still error when uploading the version2.Instead, I just download the Inventor 2018 version of the model, then open the '.ipt' file using Autodesk fusion 360 software.
then it works.

And I think there is some wrong with the model v172  in https://a360.co/2CPZoto because it has became like this now:

------------------ 原始邮件 ------------------
发件人: "Aaron Schultz"<notifications@github.com>;
发送时间: 2019年7月31日(星期三) 中午12:43
收件人: "Nate711/StanfordDoggoProject"<StanfordDoggoProject@noreply.github.com>;
抄送: "csliu"<773849295@qq.com>;"State change"<state_change@noreply.github.com>;
主题: Re: [Nate711/StanfordDoggoProject] Error when open the fusion modelversion2 (#29)

I see that you have closed this issue. Did you find a solution to it? Someone else is having the same problem, but I cannot find anything wrong in the CAD.

—
You are receiving this because you modified the open/close state.
Reply to this email directly, view it on GitHub, or mute the thread.

maxsu, 2019-09-18:
@CS4Liu, @CrazyAZ - this is still an issue with the project. It's caused by corrupted Simstudies: See the last post of [#34](https://github.com/Nate711/StanfordDoggoProject/issues/34), as well as this fusion 360 [support thread](https://forums.autodesk.com/t5/fusion-360-support/stanford-doggo-public-link-upload-issue/m-p/9006809/highlight/true) for a repaired version of the file.

I'd like to get this issue resolved. Can I join the CAD team?

Closed 2019-07-31.

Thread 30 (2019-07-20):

Question about the custom frabricated Parts

CS4Liu, 2019-07-20:
Hello, I'm on the road to rebuild Doggo. And I have bought a 3D printer, but when I download the model of the custom parts. There are two files that seem not available. They are "Outer Coaxial Tube (Set of 4)" and "3D printed 48T outer pulley":
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

The files in these two links are ".temp"(seems not work), where can I get this two complete files?

PS: Would the Doggo works well if I use PLA to print all the 3D printed parts?

Thank You!!

Closed 2019-07-22.

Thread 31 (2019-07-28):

Error when we download a zip or clone the project, version 2

mseedman, 2019-07-28:
We have been unable to download a zip or clone the project.  Many of the folders are empty.

mseedman, 2019-07-28:
Error code from fusion: Leg Linkage Assembly.f3d could not be uploaded due to access denied. This occurs when you have lost access to the project of references. Please contact the project moderator for assistance

CrazyAZ, 2019-07-31:
The folders are empty because you haven't downloaded the submodules. In order to download them you need to run these two commands:
`git submodule init`
`git submodule update`

We are looking into the permissions error with the CAD, but don't know the cause yet.

Closed 2019-10-20.

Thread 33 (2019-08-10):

Wiring Schematics Redux

maxsu, 2019-08-10:
In issue #18 @bestjinx asks whether there is a circuit schematic for doggo. In issue #20, @helloplanet contributed a tentative pinout. I'd like to address the lack of schematic, and propose a way forward towards a community contributed schematic.

In particular, I'd like to entertain the theory that:
1. There has simply been no need for a formal cad schematic so far / a schematic has been considered out of scope
    - The system uses a breadboard, and has a pretty simple communication pin layout which is encoded in the firmware
    - This would be clear to the designers and people conducting a serious review
    - It would however be a great benefit for hobbyists / students
    - But! it would be a _substantial_ labor
    - As such it may be out of scope for doggo designers' current goals

Continuing this line of thought:

2. We may have an opportunity to contribute a cad diagram as a community. Some notes towards this:
  a) The teensy's pinouts for the [AS5047D-TS_EK_AB  IMU](https://www.mouser.com/ProductDetail/ams/AS5047D-TS_EK_AB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) are mapped [here](https://github.com/Nate711/Doggo/blob/2e710121f618b006577a700c81c319086a46a366/src/config.h#L44-L48). Note that the current generation doggo BOM does not include the IMU.
b) Teensy -> Odrive serial ports get mapped [here](https://github.com/Nate711/Doggo/blob/32adf4e5ffb48af696df22e234c95e03d725bcf6/src/globals.cpp#L13-L16).
 c) The Xbee is connected to the Teensy via the teensy's USB host port, and simply relays USB serial commands to the Teensy (see [this](https://github.com/Nate711/Doggo/blob/master/src/usb_serial.h))

3. Last, but certainly not least, the electrical diagram we find in the [Doggo Paper](https://arxiv.org/ftp/arxiv/papers/1905/1905.04254.pdf) shows us that b) and c) are the only data connections in doggo. The rest of the connections are power connections that we can infer with relative ease.

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

A formal CAD model would be a crucial step in reducing hobbyist/student expertise barriers, and would open the way for a fully integrated open source circuit board with no breadboard component.

@bestjinx, @kigerzh, @HelloPlanet  - Would you three be interested in helping an effort to reverse engineer the circuit schematic, if necessary?

@Nate711 @CrazyAZ  - what would you guys recommend here? Can we get your blessings on an open schematic for doggo?

maxsu, 2019-08-10:
Next steps:

1. Agree on a circuit design software (eg, KiCad, Autodesk Eagle, etc.)
2. Add part IDs to the electronic parts in the BOM
3. Import component pinouts into PCB-CAD
4. Build the component netlist
5. Layout and annotate the schematic, title block, etc
6. Version and commit the schematic to the project.

Nate711, 2019-08-26:
Hi Maxsu, thanks for opening this issue. If you guys want to make a schematic we'd love it and would happily check it. We are unfortunately maybe too busy to create as nice a circuit design as you might like. However we could make a pin-to-pin table of connections if that would suffice.

niranjan1997, 2020-06-05:
Hi Nate, it would be great if you can provide the pin  to pin table

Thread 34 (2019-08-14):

Issue with V2.0 CAD

maxsu, 2019-08-14:
Hi all,

It looks like Doggo's v2 CAD model is experiencing some issues - From the web viewer:

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

Description:
- There are left-translated copies of the right motor & shaft assemblies and the forward sheet metal component
- Affected items are translated forward relative to the side plates and legs
- Affected items are canted WRT the right side plate, so that their right mating faces are vertical
- All other parts and sub-assemblies appear properly positioned

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

The DXF export of the v2 cad shows the same issues. I could not check the file in A360 due to the "Access Denied" issue.

I could eventually rebuild the model's assembly tree if necessary. Before I do that:
- Can anyone else confirm the issue?
- If the issue is more than an A360 cache glitch, is a repaired model available?

mseedman, 2019-08-14:
I can confirm the issue.  Michael

Nate711, 2019-08-26:
Can you try checking again? I re-computed the model. I really have no idea why Fusion does this....

maxsu, 2019-09-02:
I've made a [post](https://forums.autodesk.com/t5/fusion-360-support/stanford-doggo-public-link-upload-issue/td-p/9000575) on the fusion 360 forums - the community may shed some light on the upload issue.

I've also found a temporary workaround. cc: @mseedman - you may find this useful.

### Workaround: Import an Inventor 2018 Model

1. Open doggo v2's [public link](https://a360.co/2CPZoto)
2. Request, Download and Unzip the Inventor 2018 model
3. Open `Full Doggo Assembly.iam` in Fusion 360
4. Fusion will prompt you to bulk-select the rest of Doggo's files

This is useful for locally inspecting the model. One issue: this doesn't add individual parts or assemblies to your project - it bundles all of doggo into a single top level assembly.

maxsu, 2019-09-07:
Good news! Autodesk support team has provided a provisional fix for the "access denied issue" (see [this thread](https://forums.autodesk.com/t5/fusion-360-support/stanford-doggo-public-link-upload-issue/m-p/9006809/highlight/true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)).  The `f3z` file contained in Jeff.Strather's `Full Doggo Assembly_Repaired.zip` loads without causing the "access denied" error.

Upon inspection, it looks like they removed the two simstudies from the project's `.f3z` file. Jeff has requested a member of the Doggo team to discuss steps to fix the original model (see the thread).

(Security note: Jeff appears to be an official member of the Autodesk team, and the file [checks out](https://www.virustotal.com/gui/file/7b64bfddaeec573c237a05f7cec86e4d40eb3dcb6a20d5a1e902fcf30e65f8c2/detection) on VirusTotal. Use your discretion here, and wait for the definitive fix if there are any concerns.)

CC: @CrazyAZ ,  @mseedman

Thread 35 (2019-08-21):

about BOM spreadsheet

youye9, 2019-08-21:
Hello, thank you very much for providing all the materials of your wonderful work.
My friend and i are going to follow you to make a Doggo, but now we meet some problems.
1.We found that the V3.5 ODrives is not available in online shop, so we plan to buy V3.6 ODrives. Which voltage version is better? 56V or 24V? Should i buy it with connectors?
2.When i checked your BOM spreadsheet, i found that there were two 2mW Wire Antenna. But in README.md you said you used a 5mW Xbee. Which one is correct?
3.The product model of minitactor in BOM spreadsheet is P115Bda while in README.md is P105, which one is correct?
4.I can't find the BNO080 IMU in BOM spreadsheet, but i believed it was used in Doggo and you forgot to write it in the BOM spreadsheet, right?
Thank you very much!

Nate711, 2019-08-26:
Hi youye,
1. 24V is ok. It's better to buy without connectors.
2. Either Xbee is ok. Just make sure you buy two of the same kind. The 2mW is preferred.
3. 115Bda is correct!
4. Thanks, I added it to the BOM. It's optional though, we only used it for backflips.

youye9, 2019-08-30:
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

Thank you very much~

Closed 2019-08-26.

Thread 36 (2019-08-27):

Motor initial position for robot gait

nucleusbiao, 2019-08-27:
Hi all,

We have prepared everything and assembled the robot. However, currently we have a problem on setting the inital motor position for starting the robot gaits.

Is there anyone knowing how to set up the intial motor position. As far as we know, every time the robot is powered on, the encoder has to calibrate the motor position. It seems that the motor intial position depends on how the legs are manullay placed at the time of powering on. Is that true? Is there a way to sufficiently guarantee that the robot legs can be automatically and correctly configured to a right place no matter how legs are placed when the robot is powered on.

Thanks a lot.

CrazyAZ, 2019-09-04:
You are correct that the placement of the legs at startup is important.  In order for our code to work all of the upper leg links must be parallel to the ground.  In addition the the linkage attached to motor0 must be the one pointing to the right.

Currently the placement of the legs at startup must be done manually. Hopefully the odrives will get support for absolute encoders soon allowing it to start in any position.

Closed 2019-09-04.

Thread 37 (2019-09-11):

Issue with StanfordDoggoOuterBigPulley.stl.step

ulaladungdung, 2019-09-11:
Hi!! Thanks for sharing the doggo project to the public. My team is currently facing difficulty in printing `StanfordDoggoOuterBigPulley.stl.step` as the file appears to be corrupted. Do you have any advice regarding this?
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
I used the download link from the shared BOM

methylDragon, 2019-09-11:
I'd like to add that I am facing a similar issue with the part.

But it also seems that the CAD file for that particular item shows a shaft instead of a 48 tooth gear?

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

maxsu, 2019-09-16:
@ulaladungdung, @methylDragon, see my feature branch for fresh STL and STEP files:

https://github.com/maxsu/StanfordDoggoProject/tree/feature/track-CAD-Files/DoggoHardware/3D%20Printed

These include all 3d printed parts in project.

maxsu, 2019-09-16:
Notes:

1. Most files are named in accordance to their part names in the CAD model, which (currently) disagree somewhat with the BOM. Hopefully this does not cause too much confusion.

2. Caution: BOM specifies [94180A333](https://www.mcmaster.com/94180A333) heat-set inserts for `StanfordDoggoOuterBigPulley`, however the CAD model is configured to use [94510A310](https://www.mcmaster.com/94510A310) screw-to-expand inserts. The CAD model requires slight revision before it can receive A333 inserts, so I recommend A310 inserts for now. Let me know if you want me to fast track a heat-set revision to you.

ulaladungdung, 2019-09-16:
Hi @maxsu Thanks so much for the help!!

And yes please, the revision would be amazing as we already have the A333 on hand. Cheers!!

maxsu, 2019-09-17:
See the [updated stl](https://github.com/maxsu/StanfordDoggoProject/blob/5ca2fe981353bd918723352c2b82fe12936ca445/DoggoHardware/3D%20Printed/StanfordDoggoOuterBigPulley.stl). Fusion version is [here](https://a360.co/31twOWO).

Be careful; I increased the minimum wall thickness by 15% (to 1.15mm), but the insert's centerline could drift during heated installation. Let me know if you need a heavier revision.

@Nate711:
Is there any other A333 version of the pulley?
Is a 1.15mm wall thickness suitable?

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

maxsu, 2019-09-17:
I reduced the height of the pulley's shoulder boss by 0.5 mm in order to accommodate the larger diameter of the A333 without altering any other parts. However,  the spacing between pulley and housing could be a problem:

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

I did a little exploration, and looks like we can restore the spacing if we aggressively recess the insert into the pulley face:
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

This also increases the minimum wall thickness:
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

Take care however; this requires a 1.4 mm translation of the outer shaft locating holes.

Nate711, 2019-10-20:
Our robot uses the A310 screw-to-expand inserts but that caused an issue where if you really tighten the set screws that go inside of the inserts and then try to unscrew those set screws, the A310 insert sometimes spins inside the plastic instead of allowing the set screw to unscrew.

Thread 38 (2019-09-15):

Revisions: V2 Motor & Shaft Assemblies

maxsu, 2019-09-15:
There are a few minor issues in the Shaft, Leg, and Motor assemblies. They range from minor disagreement with the BOM, to a construction tree error.

I'll start with the simplest first:

## Leg Assembly:
- [ ] Set Screws missing from assembly.
       - Part #: `94180A333` Cup Point Set Screw
       - This item is present in BOM, but not assembly.

## Motor Assembly:

- [ ] `Pulley Bracket` missing from BOM
       - This part is present in assembly, but not BOM.
       - Part material needs specification: 3dp or Aluminum

- [ ] Lower AS5047 needs mounting nuts
       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

- [ ] Misaligned bolt in upper AS5047 plate
       Part:  `single plate design > Screws  > 92095A181 (1):17`
   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

- [ ] Phantom component: `Pulley Brace (Aluminum):1 & 2`
       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

- [ ] Phantom bodies
       Parts: `REV 2 Small Pulley Print`, `REV 2 Small Pulley LONG Print`
       Bodies: 1 & 2

## Coaxial Assembly
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

- [ ] 1. Inner shaft: Unintended hole
- [ ] 2. Outer shaft: Unintended 0.5mm web
- [ ] 3. Inner shaft: Missing dowel pin
           - This part is present in BOM, but not assembly
           - Part number: `93600A455`
           - Needs interference fit sizing

  - Suggested Fix (file available upon request):
     - 1. I've removed the inner shaft from the extrude feature which creates the outer shaft's set screw hole
     - 2. I've perform the outer shaft set screw feature after the outer shaft revolve feature which creates the bearing shoulder
     - 3. I've added a dowel pin hole hole in the inner shaft, and extend the inner shaft shaft 2 mm past the pulley body as a part holding feature during dowel pin installation
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

[ ] `Outer Big Pulley`: BOM collision
    - Assembly has: `94510A310` (Brass Screw-to-Expand Inserts)
    - BOM has: `94180A333` (Heat-Set Inserts)

[ ] Inner shaft spacer missing from BOM
    - Assembly Name: `Spacer (1)`
    - Needs material spec: 3dp or 16.6x12.6x1 Steel washer

[ ] Duplicate Component: `SDP_a_6a53m048nf0908` and  `Rev 2 SDP_a_6a53m048nf0908:1` are identical

Nate711, 2019-09-21:
I think I fixed the CAD issues. Check it out when you have a chance!

maxsu, 2019-09-24:
@Nate711 I thank you for your response and continued work on Doggo. I'm sad to say that the cad model still experiences the `access denied` error (featured in #31, #29, #34):
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

This error means nobody can import doggo's design from its public link. It's really important that we get that problem fixed and restore public access to doggo's design. Thanks!

Fusion 360 support identify the problem in this F360 [forum link](https://forums.autodesk.com/t5/fusion-360-support/stanford-doggo-public-link-upload-issue/m-p/9006809/highlight/true) :
- `Single Plate Design` and `Leg Linkage Assembly` become corrupt in translation to `.f3z`
- In the short term, removing the simstudies appears to fix the model
- Support has asked for feedback to fix the real problem

Nate711, 2019-10-04:
@maxsu Hi Max, thanks for specifying which parts were corrupt. I had seem the issue before but didn't know which simulations to delete. I got the downloaded fusion archive to upload properly on my computer. Can you check too? Thanks

maxsu, 2019-10-06:
Unfortunately I'm still having the same issue. I used the latest url from `DoggoHardware/FullCAD`, which is https://a360.co/30j7ANn

The archive has the two bad simstudies present in previous versions of the file:
`488f29e2-8a9f-450c-9303-3dc281e19bad.simstudy`
`2a44713a-4246-48b2-9885-3395ac1c1014.simstudy`

Perhaps you are looking at a different URL? Can you check if your archive has simstudies?

 1. Rename the `full CF.f3z` into `full CF.zip`
 2. Open the zip and check for the simstudies above

Nate711, 2019-10-08:
@maxsu So I see that the simstudies are still present. But I've deleted them in both Fusion 360 parts. Is there anything left I can do?

maxsu, 2019-10-10:
@Nate711 sorry for my late response. You can talk to F360 support member jeff.strater [here](https://forums.autodesk.com/t5/fusion-360-support/stanford-doggo-public-link-upload-issue/m-p/9006809/highlight/true). I'd let him know you've tried deleting the sim-studies with no luck - he can work with the F360 dev team to get to the bottom of the issue.

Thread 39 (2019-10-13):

Encoder mount doesn't fit

Kevinskwk, 2019-10-13:
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
As shown in the image and the CAD file, there is no space between the upper motor and the side panel, which results in no space to put nuts to fix the encoder mount.

Kevinskwk, 2019-10-17:
Okay we managed to solve it by putting inserts into the 3d printed mount such that no nuts are needed.

Closed 2019-10-17.

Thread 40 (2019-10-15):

How to calibrate the legs automatically

Ginot-Joah, 2019-10-15:
As using ABI interface on encoders , the leg can only be calibrated to a spectical(actually I put it at) position manually before powering on , or it will keep the position when power is on as its start position and never go to the ideal one . However , the odrive firmware did not have SPI support .
So how to solve it .....

Nate711, 2019-10-20:
We use a physical jig to make sure the legs are in alignment before turning the robot on and letting the ODrives do their encoder offset search.

Closed 2019-10-20.

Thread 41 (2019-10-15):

Issue with the Odrive custom firmware based on version 0.4.0

SunHR-SWJTU, 2019-10-15:
Hello Nate711,

I flashed your Odrive custom firmware based on version 0.4.0, but it sometimes caused the uncontrolled spinning of some motors. These motors will spin up to full speed if I use odrv0.axis0.requested_state = AXIS_STATE_CLOSED_LOOP_CONTROL. I tested the firmware of version 0.4.0-master, it still happened. But after I flashed version 0.4.11-master, it works. So maybe some problems existed in version 0.4.0.

I'm very sorry to ask if you can migrate your changes to version 0.4.11. Or is there another way to solve this problem?

Thank you so much.

Ginot-Joah, 2019-10-18:
Hello SunHR-SWJTU

I have ever seen that Nate711 reply in odrive forum declaring he just have a bit change in odrive firmware.So maybe you should pay your attention on the forum.

In my opinion , I suppose he only change the part about outer loop  trajectory control for adapting the theta and gamma from teensy .

I think your issue is more about the index search which would impact the inner loop trajectory control . There is idx_search_speed in file config that it is used in Encoder::run_index_search() . And this function will make the value into inner loop , as a result , if the this value is too big , the inner current control loop would not convergence.

In a word , maybe close the index search or reduce its speed will work . If it does not , look carefully into this two loop .

Hope it would help for you .

SunHR-SWJTU, 2019-10-19:
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

Thanks for your suggestion. But I'm afraid that Doggo wouldn't work properly after I disabled index search. Anyway, I will try your suggestion. Thanks again.

SunHR-SWJTU, 2019-10-19:
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

Thanks for your suggestion. But I'm afraid that Doggo wouldn't work properly after I disabled index search. Anyway, I will try the method you suggested. Thanks again.

Nate711, 2019-10-20:
Could you tell me more about your problem? I was never able to get the index pin search to work with our firmware. I think they did fix it though in future releases.

Ginot-Joah, 2019-10-22:
I think I didn't make the encoder clear. These days I was trying to turn its leg at the best position automatically when powering on by itself. That is a problem about the absolute position give by the encoder.

At first I think the ABI encoders can not be absulote .However, I am wrong. The index search is only about it. In fact, the sinal Z should be responsible for this absolute position via the index search function. I verify it by Suspending the Z pin and set index search into false, still running well.

As a result ,I think the Z pin have no sinal but I dont have oscilloscope to monitor it. If it has no sinal,  without questions, it will spin uncontrolledly. And I notice the encoders used in doggo can be a complete absolution by burning its OTP memory but I don't konw if it is neccessary.Hope someone would give me a hand.

By the way , the run_index_search do the same thing as run_closed_loop_control_loop until running this code....
`axis_->run_control_loop([&](){
        phase = wrap_pm_pi(phase + omega * current_meas_period);

        float v_alpha = voltage_magnitude * arm_cos_f32(phase);
        float v_beta = voltage_magnitude * arm_sin_f32(phase);
        if (!axis_->motor_.enqueue_voltage_timings(v_alpha, v_beta))
            return false; // error set inside enqueue_voltage_timings
        axis_->motor_.log_timing(Motor::TIMING_LOG_IDX_SEARCH);

        // continue until the index is found
        return !index_found_;
    });`
It just calculate the v_alpha and v_beta directly and run_closed_loop_control_loop use current_setpoint and phase to do this thing. This two value is about the FOC current control and it finally control the motor through SVPWM. As a result , I don't think this will go wrong as they two are just different in the run_control_loop shown above.......

If there's something wrong, hope you can point out, thanks.

SunHR-SWJTU, 2019-10-23:
> Could you tell me more about your problem? I was never able to get the index pin search to work with our firmware. I think they did fix it though in future releases.

Before I saw the BOM, I used AS5047P, Odrive 3.5-48V and MN5212 KV340 to repeat your work. AS5047P communicated with ODrive by ABI pins. After I assembled the components, I flashed your custom firmware into the ODrive. Then I configured the parameters according to the procedure in Nate711/ODrive/tools/doggo_setup.py. (Because AS5047P was used, <axis>.encoder.config.cpr was asigned to 4000.) After these steps were done, I powered the Odrive with a 6s-LiPo battery, the motors span up to very high speed. I was very confused. Then I did several tests.

1. I wonded if the configuration leaded to this problem. So I configured the parameters according to ODrive Documentation. The problem remains.
2. Then I wonded if it is the custom firmware that caused this problem. So I flashed the firmware of 0.4.0-master into the ODrive, and configured the parameters according to ODrive Documentation. The problem remains.
3. Then I found that the BOM was provioded. So I used AS5047D to replace AS5047P, and configured <axis>.encoder.config.cpr back to the default 2000 (same as Nate711/ODrive/tools/doggo_setup.py). The problem remains.
4. I then wonder if this problem has been fixed in the new firmware release. So I flashed the firmware of 0.4.11-master into the ODrive, and configured the parameters according to ODrive Documentation. It works!

So I think probably some bugs in the firmware of version 0.4.0 caused this problem. It should be noted that this problem does not occur every time, but very frequently. And in version 0.4.11, this has never happened. I tried to modify the firmware of 0.4.11 according to your changes in 0.4.0 but failed for lack of understanding about ODrive. Considering that you are familier with the source code, I will be very appreciated if you release a custom firmware based on the latest version.

By the way, if index search is disabled, how to configure other parameters? Forgive my ignorance please, but if there were a configuration guide, it would be easier for researchers in other disciplines to duplicate Doggo.

Thanks a lot!

danbo2, 2019-10-24:
Hi SunHR,

Have you implemented the RobotDog ? We are repeating it but meet some issues when assembly. Can you give me your email address ?@SunHR-SWJTU
Thanks,
Yiyi

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

Hi SunHR,

Have you implemented the RobotDog ? We are repeating it but meet some issues when assembly. Can you give me your email address to discuss some issues ?
Thanks,
Yiyi

SunHR-SWJTU, 2019-10-25:
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

My email address is sunhaoran126@126.com.

Ginot-Joah, 2019-10-25:
@SunHR-SWJTU
Look at the function Controller::update, for how odrive make the control.Here are the describtion given by madcowswe:

Purpose:
Motor force = - kp * (position - desired position) - kd * velocity
We currently have:
current = vel_gain * (desired_vel - actual_vel) and
desired_vel = pos_gain * (desired_pos - actual_pos).
Substitute in desired_vel into the 1st formula, and you get:
current = vel_gain * (pos_gain * (desired_pos - actual_pos) - actual_vel)
Multiply in vel_gain:
current = vel_gain * pos_gain * (desired_pos - actual_pos) - vel_gain * actual_vel
And now you can see this is the exactly the same control law that you wanted, if you set:
vel_gain * pos_gain = kp
vel_gain = kd

Now you look at Nate711's function Controller::update, he make it in an elegant way. He use alpha and beta to express the position and velocity of the two axises. It corresponds to the p gain and d gain, and plus them together for current value!! So he can control two axises at the same time! It's billiant!

However, he use a value "pll_vel_" as input which is assigned in a PLL loop of Encoder::update. Is it the axises' velocity? I don't know..
Emmm, replacing the Controller::update in 0.4.11 by Nate711's  Controller::update may work. But the new firmware had change pll_vel_  into vel_estimate_......

SunHR-SWJTU, 2019-10-28:
@Nate711 @Ginot-Joah
Thank you for your kind help. I run the doggo_setup.py and the all motors worked.

Previously, after a failure to run the script, I had opend it and should set up Doggo according to the bare_bones_calibration() which disabled the index search, because the actual calibration in main() is it. However I seemed to take it for granted that full_calibration() is better than bare_bones_calibration(), so I had use full_calibration() which enabled the index search, thus the problem occured. It has been verified that, as you said, uncontrolled spinning is related to the index search.

Thanks again! I'll continue to do the following work to repeat Doggo.

Ginot-Joah, 2019-10-28:
@SunHR-SWJTU
What you do is just evaded the index search, but I am afraid that the problem should be solved. I think it is the key to stand it up by itself rather than adjusting its legs by hand before powering up.

akrolic, 2021-06-19:
Hey @Ginot-Joah,
I agree with you, I would also like to find a solution to this issue. Have you spent anytime trying to come up with a solution since your posts from 2019? Please let me know because I am at a point know where I will begin looking at migrating towards a newer firmware version and solving the encoder absolute index problem would be a priority. From what I understand the latest odrive firmware has support for absolute encoders, so migration should solve this problem more or less on its own.

Thanks!

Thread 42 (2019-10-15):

Missing components in item list

danbo2, 2019-10-15:
Hi,

When we repeat the dog, we can not find some components in item list.
1. Inner Leg Shaft
2. Harness Mount
They all can be found in fusion CAD, but not in item list.

Thanks,
Yiyi

danbo2, 2019-10-22:
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

danbo2, 2019-10-22:
The first picture is Harness Mount and the second is Inner Leg Shaft.

Closed 2020-02-25.

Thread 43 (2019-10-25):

Motor Spacer

danbo2, 2019-10-25:
Can someone tell me whether the Motor Spacer is in purchasing list.
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

Kevinskwk, 2019-11-13:
Hi there! I also didn't find this spacer in the purchasing list. Alternatively, we laser cut the spacer out of acrylic sheet when we made it. I don't actually recommend using acrylic since this part seems to be load-bearing and this is only our temporary solution. I think you should consider using stronger material if possible. Cheers!

danbo2, 2019-11-19:
@Kevinskwk  Thanks for your help. I have downloaded the fusion 3D model and extracted this part for 3D printing.

Closed 2019-11-19.

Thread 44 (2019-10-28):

How to let the Motor Run？ I just want test the system can run success？

xuankaicheng, 2019-10-28:
Dear Nate711
I just want test the system can run success，next is my operating。But the motor can't run.
Witch of the parameters is necessary to let the motor run?
I use one odrive3.5-24V(Flash firmware success)(tup.config)
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

One motor（is MN5212-KV340） connent to M0,one as5047d lock on moto and connect the M0 ABZ. use the  power source is 150W。I send 'H' command(Teensy3.5 can receive the command)。
Odrive connet Teensy3.5 with UART1。
But the  motor don't run. Some of parameters which should i set can let the motor run.

AS5047D  Lock on the motor The ABI connect the ODrive M0 ABZ;Motro connect M0。
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

AS5047D I PIN is always low
the AB pin wave in picture。
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

 I use the Teensy3.5(#define IMU_VERBOSE 1) power on,Receive the message
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

next send HOP command，receive the message
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

Thank You!!!

xuankaicheng, 2019-10-30:
I find the answer use doggo_setup.py script,I will try it.

xuankaicheng, 2019-10-31:
Hi Nate711
I use doggo_setup.py configure the odrive successs。Power On calibration motors and encoders success the motors can run.
(Teensy3.5) RX1 -- (Odrive3.5-24V )GPIO1
(Teensy3.5) TX1 -- (Odrive3.5-24V )GPIO2
Teensy3.5 connect Odrive success(I USE multimeter test it)
I use serials tool send command H,receive Teensy3.5 message,but motors can,t run.
(Question Teensy3.5 how to configure can let motors run witch command).
The power outout 24V  5A。

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

Another question is the BOM display the odrive is 24V version,but the github say you use the ODrive is 48 whitch is the right version of ODrive.

caobencheng, 2019-11-14:
Hi Nate711, and xuankaicheng, I met the same problem just as xuankaicheng met. I tested the Odrive board with doggo_setup.py, and it looks good. However, I connect the Odrive and the Teensy board on UART 1, and I run the Teensy, I found the motor just not run and no any response. I use oscilloscope to check the signals on Pin0(RX1) and Pin1(TX1) of Teensy, the signals keep high without any changing. So there is no UART data sent on Pin1 and no data received on Pin0. What is the reason that no data sent on UART 1 of Teensy? thanks. ben

niranjan1997, 2020-09-26:
Hey @xuankaicheng , did you solve this issue ? even I have the same issue please help me fix this. thank you.

Closed 2019-11-11.

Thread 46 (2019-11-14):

No data sent on Uart1 to Odrive

caobencheng, 2019-11-14:
Hi, Nate711, and the team, I met a problem and do not know why.I have tested the Odrive board with doggo_setup.py, and it looks good. I connected one Odrive board with one motor and the Teensy board through Uart1, then power on. I run the Teensy, and then it started with the led flashing and command line prompts normally. However, the motor has no any movings
or actions. I send command H, or T, or others, still the motor has no response. I use oscilloscope to check the signals on Pin0(RX1) and Pin1(TX1) of Teensy, the signals keep high without any changing all the time. So I can confirm that there is no UART data sent on Pin1 and no data received on Pin0. What is the reason that no data sent on UART 1 of Teensy? Thanks. BEN

caobencheng, 2019-11-15:
Hi, Nate711, and the team, I have solved the problem. Right now the TEENSY can successfully control the odrive board and the motor can run according to the E(dancing), T(Trot), R(reset) and S(stop) commands. Thanks. BEN

UncleMask, 2020-07-23:
I have the same problem, and my LED is not bright, I was wondering how you solve this problem

caobencheng, 2020-07-23:
Hi, UncleMask, I found the led port type will be changed by IMU function failing,so I  move the calling of "BlinkThread" at last in  chSetup(). You can try.

UncleMask, 2020-07-24:
Yes, I solved the problem after seeing your another issue. Thanks very much

发件人: caobencheng<mailto:notifications@github.com>
发送时间: 2020年7月24日 0:51
收件人: Nate711/StanfordDoggoProject<mailto:StanfordDoggoProject@noreply.github.com>
抄送: UncleMask<mailto:SIMON.R1995@OUTLOOK.COM>; Comment<mailto:comment@noreply.github.com>
主题: Re: [Nate711/StanfordDoggoProject] No data sent on Uart1 to Odrive (#46)

Hi, UncleMask, I found the led port type will be changed by IMU function failing,so I move the calling of "BlinkThread" at last in chSetup(). You can try.

―
You are receiving this because you commented.
Reply to this email directly, view it on GitHub<https://github.com/Nate711/StanfordDoggoProject/issues/46#issuecomment-663116027>, or unsubscribe<https://github.com/notifications/unsubscribe-auth/AEZVVJRJJZEVEKR2CURDLXLR5BTCFANCNFSM4JNGMGHQ>.

niranjan1997, 2020-10-03:
> Hi, Nate711, and the team, I have solved the problem. Right now the TEENSY can successfully control the odrive board and the motor can run according to the E(dancing), T(Trot), R(reset) and S(stop) command. Thanks. BEN
Hello @caobencheng, I have the same exact problem, may I know how did you resolve this issue. Thanks in advance.

qw7798965, 2021-01-08:
Hello @caobencheng, I have the same exact problem, may I know how did you resolve this issue. Thanks in advance.

Closed 2019-12-05.

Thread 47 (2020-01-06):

The leg connect with Odrive is important，so i want to know, my connect is right?

xuankaicheng, 2020-01-06:
Dear everyone!
        I build up one doggo,i want to know the legs and the IMU direction  is connect right.The connect is the next picture.
Thanks！

The IMU direction picture.

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

The legs connect picture.

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

zhngfeichen, 2021-10-13:
i do not konw

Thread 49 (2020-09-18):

doggo_setup.py doesn't work?

15521131907, 2020-09-18:
I use ODrvie V3.6-56V and burn the modified firmware. When I run the doggo_setup.py script, it just runs the motor calibration (beep~) and exit.  It seems haven't finished all the programs. Should it still have encoder calibration?. I check the errors in odrivetool, no error.

15521131907, 2020-09-25:
I found that it should use full_calibration(app_shutdown_token) rather than bare_bones_calibration(app_shutdown_token, reset=False).

Closed 2020-09-25.

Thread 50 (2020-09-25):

Teensy serial monitor is blank

niranjan1997, 2020-09-25:
Hello Nate, I have tried building the firmware using Platformio on both Vs code and Atom. The build was successful without errors and uploaded to the board. Even after successful build and upload. Nothing shows up in the serial monitor, and the led on board is not blinking. what might be the cause? please help me fix this. I am on the verge of completing this project.

RajPShinde, 2020-09-26:
If you are not using the Xbee, comment #define USE_XBEE in config.h

niranjan1997, 2020-09-26:
yes, I am using Xbee but according to the code, the Led on the teensy board should glow if the code is properly uploaded to the board right? The led on my teensy isn't glowing even after successful build and upload.

Closed 2020-10-03.

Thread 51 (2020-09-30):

Belts Skipping teeth

RajPShinde, 2020-09-30:
@Nate711 @pslade2 @CrazyAZ I just completed the assembly. The issue is the belts are skipping teeth when I try to Trot using default parameters. The robot does stand on its own without any issue, the skipping only takes place at high velocities. I am using the provided 3D Printed Brace and HTD 3M Belts. Can you please help me?

akrolic, 2021-06-19:
Hey @RajPShinde,

I hope you have been able to resolve this issue, but I can offer some advice from our teams experience. We were able to tension the belts by loosening the drive shaft assembly and pulling it away from the motors. With it pulled away and the belts in tension, you can have someone else  tighten the assembly in place. This has worked for now, a future improvement would be to ensure that the assembly will not shift from the final tensioned position.

If your issue is not that the belt isn’t tensioned enough, then perhaps your belts could be misaligned. We solved our misalignment by adding appropriate spacing to the distance between the two belts. We also varied the height of the drive shaft a bit using washers to get a perfect alignment.

Let me know if you need any help!

daydayupzhang, 2022-04-20:
你好，我已经收到你的来信。

Closed 2022-04-20.

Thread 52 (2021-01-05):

Motor movement failed with

DBAjust115, 2021-01-05:
The odrive arduinotest test can run the motor successfully. After burning the whole file, the test cannot be carried out (I tested a single odrive with two motors, without IMU module). Is it possible that the IMU module needs to be added?

ducktrA, 2021-03-04:
Hi i am chasing you and just flash the teensy. I dont have the solution. But you are not alone.

ducktrA, 2021-03-12:
@DBAjust115 how did you compile the Odrive? Did you use an older toolchain?

I am running into a problem when using std::enable_if

*  4) arm-none-eabi-g++ -std=c++14 -c communication/communication.cpp -DHW_VERSION_MAJOR=3 -DHW_VERSION_MINOR=5 -DHW_VERSION_VOLTAGE=24 -DUSB_PROTOCOL_NATIVE -DUART_PROTOCOL_ASCII -D__weak="__attribute__((weak))" -D__packed="__attribute__((__packed__))" -DUSE_HAL_DRIVER -DSTM32F405xx -mthumb -mcpu=cortex-m4 -mfpu=fpv4-sp-d16 -mfloat-abi=hard -Wall -Wfloat-conversion -fdata-sections -ffunction-sections -g -gdwarf-2 -Og -ffast-math -fno-finite-math-only -IDrivers/DRV8301 -IMotorControl -Ifibre/cpp/include -I. -IBoard/v3/Middlewares/Third_Party/FreeRTOS/Source/portable/GCC/ARM_CM4F -IBoard/v3/Middlewares/Third_Party/FreeRTOS/Source/include -IBoard/v3/Middlewares/Third_Party/FreeRTOS/Source/CMSIS_RTOS -IBoard/v3/Middlewares/ST/STM32_USB_Device_Library/Core/Inc -IBoard/v3/Middlewares/ST/STM32_USB_Device_Library/Class/CDC/Inc -IBoard/v3/Drivers/STM32F4xx_HAL_Driver/Inc -IBoard/v3/Drivers/STM32F4xx_HAL_Driver/Inc/Legacy -IBoard/v3/Drivers/CMSIS/Device/ST/STM32F4xx/Include -IBoard/v3/Drivers/CMSIS/Include -IBoard/v3/Inc -I. -IDrivers/DRV8301  -o build/communication_communication.cpp.o
In file included from /usr/include/newlib/c++/9.2.1/bits/move.h:55,
                 from /usr/include/newlib/c++/9.2.1/bits/stl_function.h:60,
                 from /usr/include/newlib/c++/9.2.1/functional:49,
                 from communication/communication.h:9,
                 from communication/communication.cpp:4:
/usr/include/newlib/c++/9.2.1/type_traits: In substitution of 'template<bool _Cond, class _Tp> using enable_if_t = typename std::enable_if::type [with bool _Cond = (0 == 1); _Tp = void]':
fibre/cpp/include/fibre/protocol.hpp:948:5:   required from 'class ProtocolFunction<Controller, std::tuple<float, float, float>, std::tuple<> >'
MotorControl/controller.hpp:158:39:   required from here
/usr/include/newlib/c++/9.2.1/type_traits:2384:11: error: no type named 'type' in 'struct std::enable_if<false, void>'
 2384 |     using enable_if_t = typename enable_if<_Cond, _Tp>::type;
      |           ^~~~~~~~~~~
 *** tup messages ***
 *** Command ID=526 failed with return value 1
 [   ETA~=<1s   ]  71%
 *** tup: 10 jobs failed.
make: *** [Makefile:14: all] Error 1

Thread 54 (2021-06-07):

Cannot Read Odrive estimated Theta/Gamma values over serial monitor

akrolic, 2021-06-07:
We are using the Odrive v3.6 flashed with the custom firmware provided in this repository and are able to perform all of the open loop gaits with no issues.
We are aware that this project was developed using the Odrive v3.5 but so far we have not had any issues with the custom firmware being incompatible with the latest Odrive hardware. However, we are running into a problem reading parameters from the Odrives and after a while troubleshooting the issue we could really use your help. Here is an overview of whats going on and what we know.

The goal is to obtain the theta and gamma values over the serial monitor.

We are printing the estimated and requested theta and gamma values using the debug.cpp file

```
void PrintODriveDebugInfo(struct ODrive odrv) {
    Serial.print(odrv.sp_theta, 2);
    Serial.print("\t");
    Serial.print(odrv.est_theta, 2);
    Serial.print("\t");
    Serial.print(odrv.sp_gamma, 2);
    Serial.print("\t");
    Serial.print(odrv.est_gamma, 2);
```

Which when printed on the serial monitor takes this format:
ODrive0:	 setpoint_theta, estimate_theta, setpoint_gamma, estimate_gamma

From the serial monitor after starting dance gait:
```
ODrive0:	0.00	0.00	0.00	0.00

DANCE
(f)req: 1.5000
step (l)ength: 0.0000
stance (h)eight: 0.1500
(d)own amplitude: 0.0500
(u)p amplitude: 0.0500
flight (p)roportion: 0.3500
(s)tep difference: 0.0000
Theta: 50.0000 0.5000
Gamma: 30.0000 0.5000

ODrive0:	0.00	0.00	1.41	0.00
```

The problem we are trying to solve is that we are not able to read back any of the estimated values from the Odrives.
We are have looked into the OdriveArduino.cpp file and  found the function responsible for constructing the messages from the serial data

```
int ODriveArduino::ParseDualPosition(char* msg, int len, float& th, float& ga) {
    // check if 1 byte for "P", 4 bytes holding encoder data, and 1 checksum byte were received
    if (len != 6) {
        return -1; // return -1 to indicate that the message length was wrong
    } else {
        // retrieve short from byte stream
        // remember that the first character is 'P'
        uint16_t th_16 = (msg[2] << 8) | msg[1];
        uint16_t ga_16 = (msg[4] << 8) | msg[3];
        uint8_t rcvdCheckSum = msg[5];

        // compute checksum
        uint8_t checkSum = 0;
        checkSum ^= msg[0]; // letter 'P'
        checkSum ^= msg[1];
        checkSum ^= msg[2];
        checkSum ^= msg[3];
        checkSum ^= msg[4];

        // DEBUG ONLY
        // Serial << "Comp checksum: " << (int)checkSum << " rcvd: " << (int)rcvdCheckSum << "\n";

        // if the computed and received check sums match then update the motor position variables
        if (checkSum == rcvdCheckSum) {
            // convert to float
            // TODO: figure out if casts are needed
            th = ((float) ((int16_t) th_16))/1000.0f;
            ga = ((float) ((int16_t) ga_16))/1000.0f;
            return 1;
        } else {
            // return -1 to indicate that the checksums didn't match
            return -1;
        }
    }
    return 1;
}
```

Then looking into uart.cpp the theta and gamma estimates would be read in when rx_state is in the READ_PAYLOAD case

```
case READ_PAYLOAD:
                //ADDED: Print statement
                Serial << "\nREAD_PAYLOAD\n";
                msg[msg_idx++] = c;
                if (msg_idx == payload_length) {
                    if (msg[0] == 'P') {
                        //ADDED: Print statement
                        Serial << "\nPROCESSING POSITION\n";
                        ProcessPositionMsg(msg, msg_idx, odrvSerial, odrvMsgOutput);
                    }
                    rx_state = IDLING;
                    msg_idx = 0;
                    payload_length = 0;
            
                    #ifdef DEBUG_LOW
                        msg_end = micros();
                        Serial << "rcvd in: " << msg_end - msg_start << " in " << loop_iters << " loops\n";
                        // NOTE: As of code 10/14/18, the average receive time was 1100
                        // And number of loop executions to get a message was 0 or 1
                    #endif
                }
```

Finally the ProcessPositionMsg is defined in the same uart.cpp where it is calling the aforementioned ParseDualPosition function from the OdriveArduino.cpp

```
void ProcessPositionMsg(char* msg, int len, HardwareSerial& odrvSerial, struct MsgOutput& odrvMsgOutput) {
    #ifdef DEBUG_LOW
        for(int i=0; i<len; i++) {
            Serial << (int)msg[i] << "(" << msg[i] <<") ";
        }
        Serial << "\n";
    #endif

    #ifdef DEBUG_HIGH
        Serial <<  "rcv at: " << micros() << '\n';
    #endif

    float th,ga;
    int result = ODriveArduino::ParseDualPosition(msg, len, th, ga);

    // result: 1 means success, -1 means didn't get proper message
    if (result == 1) {
        // Update theta and gamma
        *(odrvMsgOutput.theta) = th;
        *(odrvMsgOutput.gamma) = ga;

        #ifdef DEBUG_LOW
            Serial << "Th,Ga: " << th << " " << ga << '\n';
        #endif

        // NOTE: it's possible that the feedback delay is wrong if an old
        // encoder reading took so long to come back that it came back after
        // another current command was sent; ie:
        // 1) Teensy sends command I1
        // 2) Teensy sends command I2
        // 3) Teensy receives reading E1
        // 4) Teensy thinks delay was E1-I2 when in reality it was E1 - I1
        // This problem won't happen if the delay is short and the control rate is small
        //
        latest_receive_timestamp = micros();
        global_debug_values.position_reply_time = latest_receive_timestamp - latest_send_timestamp;

        #ifdef DEBUG_HIGH
            Serial << "Done prs at: " << micros() << '\n';
            Serial << "Reply time (uS): " << global_debug_values.position_reply_time << "\n";
            // NOTE: As of 7/7/18 code, around 1500us from send to receive
        #endif
    } else {
        #ifdef DEBUG_LOW
            Serial.println("Parse failed. Wrong message length or bad checksum.");
        #endif
    }
}

```

We placed in some print statements in the ProcessSerial function to determine which state it is in and see when it reaches the READ_PAYLOAD case but it never did. We turned on the robot, sent the E command (performed the gait for about ~20 sec), sent the S command, and then when we turned off the ODrives the threads finally entered the while loop. The while statement condition is:
`while (odrvSerial.available()) `
So we are confused why the serial isn't available until the ODrives are turning off.

As a side note, we also were not able to write any IMU values to the SD card. We have formatted the card to FAT32 and can see the created datalog##.csv files but they are 0kb (nothing is being written to the card and stored). I can create a separate issue for that though, just wanted to mention it here just incase.

akrolic, 2021-06-19:
Hello again, we are still actively trying to fix this problem. It’s necessary for our project to be able to read back data from the odrives. We have tried several different changes to the code to try to find a work around but none have been successful. What we learned is that we are able to receive some rx bytes back only after the odrives have been turned off. The received serial messages are a series of special characters and noise, nothing like what should be read out.
Our teensy, xbee, and imu are all being powered from a separate battery than what the odrives are being powered by. We initially had issues when all devices were powered by one battery. A ground loop was completely preventing any open loop gait commands from being sent to the odrives over the serial connection from the teensy.

I will make a separate post on the odrive forum to see if anyone else has experienced similar issues when controlling their motors.

@CrazyAZ or @Nate711 do either of you recall if you were able to read the estimated theta and gamma messages back from the odrives?

Thank you in advance for any support you can provide to our team.

akrolic, 2021-07-02:
Issue has been resolved!

The problem was not on the teensy side, but rather on the Odrive firmware side. In hindsight this makes sense, but it was a bit of a journey to come to the realization.

In /Odrive/Firmware/communication/ascii_protocol.cpp
The function 'ASCII_protocol_process_line' contains the following lines of code
```
    } else if (cmd[0] == 'C') { // dual current control
        float motor0_cur_sp, motor1_cur_sp;
        int result = parse_dual_current(cmd,len,motor0_cur_sp, motor1_cur_sp);

        if (result != 1) {
            respond(response_channel, use_checksum, "Failed on parse or checksum: ");
            respond(response_channel, use_checksum, cmd);
        } else {
            // set motor currents
            axes[0]->controller_.set_current_setpoint(motor0_cur_sp);
            axes[1]->controller_.set_current_setpoint(motor1_cur_sp);

            // IMPORTANT CODE: send motor encoder readings in response
            send_motor_positions(response_channel);
        }

    } else if (cmd[0] == 'P') { // coupled control
        float theta_sp, gamma_sp;
        int result = parse_dual_current(cmd,len,theta_sp, gamma_sp);

        const float MULTIPLIER = 1000.0;

        theta_sp /= MULTIPLIER;
        gamma_sp /= MULTIPLIER;

        if (result != 1) {
            respond(response_channel, use_checksum, "Failed on parse or checksum: ");
            respond(response_channel, use_checksum, cmd);
        } else {
            axes[0]->controller_.set_coupled_setpoints(theta_sp, gamma_sp);
            axes[1]->controller_.set_coupled_setpoints(theta_sp, gamma_sp);
        }
    } else if (cmd[0] == 'S') { // coupled control with gains
        float sp_theta, kp_theta, kd_theta;
        float sp_gamma, kp_gamma, kd_gamma;

        int result = parse_coupled_command(cmd, len, sp_theta, kp_theta, kd_theta, sp_gamma, kp_gamma, kd_gamma);

        if (result != 1) {
            respond(response_channel, use_checksum, "Failed to parse coupled command: ");
            respond(response_channel, use_checksum, cmd);
        } else {
            axes[0]->controller_.set_coupled_setpoints(sp_theta, sp_gamma);
            axes[0]->controller_.set_coupled_gains(kp_theta, kd_theta, kp_gamma, kd_gamma);
    
            axes[1]->controller_.set_coupled_setpoints(sp_theta, sp_gamma);
            axes[1]->controller_.set_coupled_gains(kp_theta, kd_theta, kp_gamma, kd_gamma);
        }
```

The version of the firmware we had was missing the "IMPORTANT CODE" which includes respond(). The definition for respond() is also contained in the same file and I will include it here for clarity.

```
void respond(StreamSink& output, bool include_checksum, const char * fmt, TArgs&& ... args) {
    char response[64];
    size_t len = snprintf(response, sizeof(response), fmt, std::forward<TArgs>(args)...);

    static uint8_t start_byte = 1;
    static uint8_t len_byte = 0;
    output.process_bytes((uint8_t*) &start_byte, 1, nullptr); // start byte
    output.process_bytes((uint8_t*) &len_byte,   1, nullptr); // byte indicating newline termination
    output.process_bytes((uint8_t*)response,   len, nullptr); // TODO: use process_all instead
    if (include_checksum) {
        uint8_t checksum = 0;
        for (size_t i = 0; i < len; ++i) {
            checksum ^= response[i];
        }
        len = snprintf(response, sizeof(response), "*%u", checksum);
        output.process_bytes((uint8_t*)response, len, nullptr);
    }
    output.process_bytes((const uint8_t*)"\n", 1, nullptr);
}
```

Now we are getting all the Theta and Gamma estimate values. Investigating this was a great learning experience for us, our next steps are to migrate all communications towards ROS

Closed 2021-07-02.

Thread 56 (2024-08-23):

Anticipation for Pupper v3 Release and Request for Updates

TinNguyen-Gianty, 2024-08-23:
Dear @Nate711,

First of all, thank you for your incredible work and dedication to the Pupper project. Your efforts have been truly inspiring, and I have been following the development of this robotic dog with great interest.

I am particularly excited about the upcoming release of Pupper v3!
The new specifications, including:
- The GIM4305 brushless motors
- Raspberry Pi 5
- The reinforcement learning locomotion policy
- The addition of the Luxonis SR depth camera
- The LCD screen for debugging and facial expressions is also a great touch.
- Roughly $1000 BOM

As someone who is eagerly looking forward to this release, I would greatly appreciate any updates or information you could provide about the progress of Pupper v3. It would be wonderful to stay informed as you move closer to the release.

Best regards,

Tin Nguyen

Closed 2024-08-23.

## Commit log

2018-09-13 Added Doggo ODrive code as submodule
2018-09-13 Updated link to full CAD
2018-10-04 New full CAD link
2019-06-03 Added Version 2.0 of the Doggo hardware.
    Version 2 includes modified 3d-printed parts that include a lot of improvements that we figured out over testing.
2019-07-31 Updated ODrive module
2019-08-05 Updated ODrive firmware
2019-10-20 update broken imu firmware
